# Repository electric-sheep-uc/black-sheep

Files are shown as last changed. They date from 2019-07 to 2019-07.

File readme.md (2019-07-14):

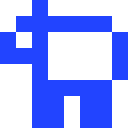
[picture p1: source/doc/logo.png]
Electric Sheep


# Electric Sheep Humanoid Robot Platform V1

This repository contains a snapshot of the
[Electric Sheep](https://humanoid.science) humanoid robotics platform as
presented in the 2019 RoboCup competition in Sydney, Australia. Please observe
the [license](LICENSE) in this repository (projects used in this release have
their own licenses either within their directories or in their source files).

We recommend that you read the technical report [here](docs/paper.pdf).

## Details

The following is intended to make understanding and using the platform easier.

**NOTE:** Vision processing will be added at a later date.

### Electronics

* [Design](docs/design-pcb.md) - Circuit design and BOM.

### Hardware

* [Design](docs/design-hw.md) - Hardware design and BOM.
* [Assembly](docs/assembly-hw.md) - Assembly of the platform.

### Source

* [Compiling](docs/compiling.md) - Compiling the `source` code.
* [Running](docs/running.md) - Running the code.

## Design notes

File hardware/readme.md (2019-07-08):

# Introduction

The initial decision is to use `openscad` [1], a CAD environment that allows
programmers to build models. There are various advantages to this model:

* The models are programmed, utilizing the majority skills of the team
* Output can be viewed at any time, with compiler warnings/errors displayed
* The source code plays nicely with `git` repositories
* Adjustments can be as simple as changing variable values
* Shapes can easily be achieved that could otherwise take a long time by hand
* Plays nicely with Linux, Windows and Mac

# Development Environment

This requires downloading `openscad` [1]. Linux users can get their latest
repository (Debian: `apt-get install openscad`).

Build models with `F6`, render the object with `F5` (in that order).

# Development Process

In general we want to build models that are justified by real measurements and
are adjustable via variables that correctly rely on one another. Improving the
accuracy of some magic value should never break any of the models if built
correctly.

If for example we decide "we want longer legs", this should be as simple as
changing a simple variable, building the models and going straight to print.
For non-experts, making changes to the models should still be very easy and
we'll likely thank ourselves in the future!

In the *future*, we should be able to simulate a robot model and leave it to
decide itself what the best simulated model is for real life performance, to
maximize some behaviour like running speed or weight.

# Building

In a Linux environment, you can run:

    bash run.sh help

This will display some available options, at the time of writing these are
building:

    bash run.sh build

To build the `.stl` files and render the `.png` files (both generated next to
the source). On the other hand, if you just want to build the STL files (which
is faster), run:

    bash run.sh build stl

**NOTE:** Files are put into a directory under `models/stl` for easier copying.
Files are given the format `<NAME>-<GIT_HASH>.stl`, where `<NAME>` is derived
from the OpenCAD filename and `<GIT_HASH>` is the first 8 characters of the
current commit. The purpose is to allow you to easily know where from random
STL files on a memory stick came from and what they are supposed to be.
Therefore, a good workflow is to pre-commit changes before running a build.

And the next option is to clean the directories:

    bash run.sh clean

Removing all binary build files (such as `.stl` and `.png`) files in the
various directories.

# References

[1] [http://www.openscad.org/](http://www.openscad.org/)

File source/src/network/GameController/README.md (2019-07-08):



# RoboCup SPL and Humanoid League GameController

This is the GameController further developed by the Humanoid League based
 on the GameController from the SPL Team B-Human

If there are any questions, please contact [sheepsy90@gmail.com](sheepsy90@gmail.de).
Please read this README carefully to avoid questions that are already answered within the document
or the [TCM](TCM.md). 

For questions regarding the protocol please check the [Wiki](https://github.com/RoboCup-Humanoid-TC/GameController/wiki).

The sources mentioned in some sections of this document are available at
[https://github.com/RoboCup-Humanoid-TC/GameController](https://github.com/RoboCup-Humanoid-TC/GameController).

### Upcoming changes (2018)

- [x] Removal of Illegal Defense and Illegal Attack
- [x] Allow Adult league to play drop in 2 vs. 2
- [x] Skip extra time in knockout games
- [x] Fix point counting on drop in challenge
- [x] Fix "GameController goes to extended time even in normal mode"
- [x] Highlight and make "current goalkeeper" changeable in UI

_See [CHANGELOG](CHANGELOG.md) for more details and history._

### Acknowledgement

The development was partially supported by the RoboCup Federation within the
calls for Support for Projects for League Developments for 2013, 2015 and 2017.

## 1. Building from Source

To build it from the source code you may use Apache Ant.
Just call "ant" in the main directory.

Building the source code requires the JDK 1.8 or newer.

## 2. GameController

### Executing the Jar

Double-click GameController.jar or run 

Usage: 
```bash
cd build/jar
java -jar GameController.jar {options}
```

    (-h | --help)                   display help
    (-t | --test)                   use test-mode - currently only disabling the
                                    delayed switch to playing in SPL
    (-i | --interface) <interface>  set network interface (default is a
                                    connected IPv4 interface)
    (-l | --league) (spl | spl_dropin | hl_kid | hl_teen | hl_adult)
                                    select league (default is spl)
    (-w | --window)                 select window mode (default is fullscreen)

### Start Dialog

Select your league. The default can be specified as a command line parameter
(see above).

Pick the two teams that are playing. They have to be different teams. If you are
practicing alone, use the "Invisibles" as second team.

SPL: The GameController automatically selects the jersey colors as defined in
the file "teams.cfg". The left teams jersey color is picked first regardless if
it has a custom jersey or not. For both teams, the first jersey color that they
have and, if picking second, that does not conflict with the jersey color of the
opponent is selected in the following sequence:

* Left team: custom 1, custom 2, blue, red
* Right team: custom 1, custom 2, red, blue

The GameController operator can switch each teams color to their secondary color
if it is necessary to distinguish the jersey colors.

You also have to select whether you play a game in the preliminaries or a
play-off game. In the preliminaries the clock will continue to run during game
stoppages and there will be no penalty shootout in case of a draw. In play-off
games, the clock will be stopped and there may be penalty shootout.

HL: You also have to select whether you play a normal game or a knock-out game.
A knock-out game will continue after a draw with two halves of extra time (if
goals were scored before) and then a penalty shoot-out if necessary. You can
also select whether teams exchange their colors in the halftime.

You can select whether the GameController should run in fullscreen mode or in
windowed mode. Note that the fullscreen mode does not work correctly on some
Linux desktops, because although they report to Java that they would support
this feature, they do not.

### Main Screen

The use of the main screen should be rather obvious in most cases. Therefore, we
only focus on the specialties.

When ever you made a mistake, use the undo history at the bottom of the screen
to correct it. You cannot correct individual decisions (except for the last
one). Instead, you can only roll back to a certain state of the game. Click the
oldest decision in the history you want to undo. After that all decisions that
would be undone will be marked. Click the decision again to actually undo it
together with all decisions that followed.

To penalize a robot, first press the penalty button, then the robot button. The
only exception is the state "Set" in playoff games, in which the "Motion in Set"
penalty is preselected and robots can be penalized by simply clicking on them
(selecting other penalties is still possible). For unpenalizing a robot, just
press the robot button.  A robot can only be unpenalized, when its penalty time
is over or when the game state changes (SPL only). Ten seconds before the
penalty time is over, the robot's button starts flashing yellow. For regular
penalties, it continues to flash until the button is pressed. Only buttons of
robots that were requested for pickup stop flashing after ten seconds and simply
stay yellow until they are pressed, as a reminder that the robot can return as
soon as it is ready. Robots with a "Motion in Set" penalty stay on the field and
will be automatically unpenalized 15 seconds after pressing the button "Play". 

Before unpenalizing a robot that was taken off the field, please make sure that
it was put back on the field by the assistant referees. For that reason, robots
are never unpenalized automatically.

To substitute a robot, press "Substitute" and then the robot that should leave
the field.  Afterwards, any of the substitutes can be activated. If the robot
that is replaced is already penalized, its substitute inherits the penalty. If
it is not, the substitute can immediately enter the field in the HL, but gets a
"request for pickup" penalty before it can enter the field in the SPL.

When pressing the big "+" (goal), "Timeout", or "Global Game Stuck", the other
team gets the next kick-off.

SPL: When the referee decides that too much game time has been lost, use the
thin "+" next to the clock to increase the game time in one-minute steps. This
is only available during stoppages of play.

### Penalty Shootout

In the penalty shootout, press "Set" and place the robots in their correct
locations. Press "Play" to start a single shot. The penalty shot is ended by
either pressing "+" for the penalty taker or by pressing "Finish" if the shot
failed. In both cases, a penalty shot ends in the state "Finished". Press "Set"
again to start the next shot.

### Shortcuts

While the GameController is running, you may use the following keys on the
keyboard instead of pushing buttons:

    Esc       - press it twice to close the GameController
    Delete    - toggle test-mode (everything is legal, every button is visible
                and enabled)
    Backspace - undo last action

only SPL

    B    - out by blue
    R    - out by red
    Y    - out by yellow
    K    - out by black
         - the new team colors implemented for RoboCup 2016 do not yet have a key
           assigned

    P    - pushing
    L    - leaving the field
    I    - fallen / inactive / local game stuck
    D    - illegal defender
    G    - kickoff goal 
    O    - illegal ball contact
    U    - request for pickup
    C    - coach motion
    T    - teammate pushing
    S    - substitute

only Humanoid-League

    B    - out by blue
    R    - out by red

    M    - ball manipulation
    P    - physical contact
    A    - illegal attack
    D    - illegal defense
    I    - service / incapable
    S    - substitute

### Adding teams to the GameController

The teams registered in the GameController are determined using the config file
located at `config/<league name>/teams.cfg` relative the the GameController.jar.
To add teams to it, lines composed of `<team number>=<team name>` may be added
to this file.
Optionally, the primary and secondary team colors may be added behind the team
name, separated by commas.

Team logos lie in the same directory as the config file with the corresponding
team number as the file name.

## 3. GameStateVisualizer

As of the 2017 RoboCup competitions, the GameStateVisualizer has been replaced
by the GameStateVisualizer mode of the TeamCommunicationMonitor.

To start it, run

`java -jar TeamCommunicationMonitor.jar --gsv`.

## 4. TeamCommunicationMonitor

The TeamCommunicationMonitor (TCM) is a tool for visualizing the data
communicated by robots during SPL games.

It serves two main purposes:

1. offering diagnostic data such as which robots are communicating on which
   team ports and whether the data that is sent by these conforms to the
   SPLStandardMessage, which is the standard communication protocol in the SPL
2. visualizing the data that was sent via SPLStandardMessages in both textual
   and graphical form.

For more info see [TCM](TCM.md).

## 5. libgamectrl (SPL)

libgamectrl automatically provides the GameController packets in ALMemory. 
It also implements the return channel of the GameController. It handles the 
buttons and LEDs according to the rules (with a few additions).

### Installation

Put the file libgamectrl.so somewhere on your NAO and add the library to your
file "autoload.ini" so that NAOqi can find it. The binary provided was built for
NAOqi 2.1.

It is also possible to build the library from source using Aldebaran's qibuild
framework. The qiproject.xml and CMakeList.txt have been placed in libgamectrl's
source folder. Just follow the instructions of the README file there.

### Usage

In your NAOqi module, execute the following code at the beginning (only once):

    AL::ALMemoryProxy *memory = new AL::ALMemoryProxy(pBroker);
    memory->insertData("GameCtrl/teamNumber", <your team number>);
    memory->insertData("GameCtrl/teamColour", <your default team color>);
    memory->insertData("GameCtrl/playerNumber", <your robot's player number>);

The team number must be non-zero. Setting the team number will reset libgamectrl
(i.e. go back to the initial state). libgamectrl will also set
"GameCtrl/teamNumber" back to zero, so it will recognize the next time your
application is started.

Setting the default team color can actually be omitted now. In that case, it is
black, i.e. the corresponding foot LED is switched off.

You can receive the current GameController packet with:

    RoboCupGameControlData gameCtrlData; // should probably zero it the first time it is used
    AL::ALValue value = memory->getData("GameCtrl/RoboCupGameControlData");
    if (value.isBinary() && value.getSize() == sizeof(RoboCupGameControlData))
        memcpy(&gameCtrlData, value, sizeof(RoboCupGameControlData));

### Deviations from the Rules

The first time the chest button is pressed it is ignored, because many teams 
will use it to let the robot get up.

In the Initial state, it is also possible to switch between "normal", 
"penalty taker" (green LED), and "penalty goalkeeper" (yellow LED) by pressing 
the right foot bumper. The state is shown by the right foot LED, and only in 
the Initial state. An active GameController will overwrite these settings.

## 6. Coach Messages

The coach broadcasts messages as defined in SPLCoachMessage.h to the UDP port
SPL_COACH_MESSAGE_PORT through the wireless network. Players are not permitted
to listen to this port. The GameController will integrate the coach messages
into the RoboCupGameControlData packet and forward them to the players according
to the SPL rules. Since coach messages must be human readable, it is assumed
that they are a zero-terminated string and all data after the first zero
character is zeroed, too.

The GameStateVisualizer also displays the coach messages.

Please note that the field "team" now contains the team number, not the color.

## 7. Protocol

For questions regarding the protocol please check the [Wiki](https://github.com/RoboCup-Humanoid-TC/GameController/wiki).

## 8. Known Issues

There are still a number of issues left:
  
- The qibuild file for libgamectrl is untested.

- The alignment of button labels is bad if the buttons are small.

- The GameController is not displaying properly on Windows-High-Res-Systems.

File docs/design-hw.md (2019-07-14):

# Design (Hardware)

For the platform, we had several requirements:

1. The platform must be low-cost. The reason for this was two-fold, firstly our
team operates on a relatively low-budget and secondly the cost-to-entry into
the RoboCup humanoid league has been gradually increasing (many platforms are
easily more than 10k euros each for a single robot). We believe that it's still
possible for low-cost entries to make a large impact in the league and hope
that this release will add to such efforts.
2. It must be easy (relatively speaking) to design and build. None of our team
are electrical engineers, for a while we didn't have any 3D designers and only
a few with any kind of background in robotics. Using off-the-shelf components
as much as possibly greatly reduces the risk in such an ambitious project.
3. The platform must be open-sourced at the end, regardless of performance in
the competition. If somebody decided to replicate our work then we need to be
able to beat our past selves in order to progress year-on-year. We also hope
that we are able to make some small contribution to the future success of the
leagues (even if this be a lesson in what not to do).

We decided on the following features:

* Raspberry Pi 3B as a main board - it offers just about enough computational
power for simple behaviours, but most importantly it's well understood and
doing low-level hardware communications is relatively simple.
* Large PWM motors for arms - As the arms are barely used in most games and
mostly used for standing after a fall, we decided if anywhere we were to use
cheaper motors, it would be here. PWM motors have a horrible habit of being
twitchy at the best of times, but especially when the PWM signal is noisy. The
cost of these motors is somewhere between a fifth and a tenth of their smart
motor counterparts.
* Smart motors for legs - We did decide that at least some accuracy was
required in the system, especially for walking. The obvious choice was
magnetically encoded smart motors that daisy-chain power and communicate on a
serial bus.
* Standard voltage step-down converters - The final voltage out of the power
PCB was much higher than we wanted for our components, so step-down is
required. We decided not to design/build our own as power system design tends
to be some form of magical art.

## BOM

The following are components used in our build:

* [IMU](https://www.banggood.com/6DOF-MPU-6050-3-Axis-Gyro-With-Accelerometer-Sensor-Module-For-Arduino-p-80862.html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)
* [Header Connectors](https://www.banggood.com/10X-2AWG-60-Core-30cm-Male-to-Male-Futaba-Plug-Servo-Extension-Wire-Cable-Parallel-Cable-p-1102386.html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)
* [Raspberry Pi 3 B](https://www.banggood.com/Raspberry-Pi-3-Model-B-ARM-Cortex-A53-CPU-1_2GHz-64-Bit-Quad-Core-1GB-RAM-10-Times-B-p-1041862.html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)
* [T60 Battery Connector](https://www.banggood.com/5Pcs-30cm-Battery-ESC-XT60-Plug-Extension-Wire-Cable-Male-Female-p-1090915.html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)
* [DC Barrel Female](https://www.banggood.com/10pcs-5_5-x-2_1mm-DC-Power-Supply-Female-Jack-Socket-p-1062018.html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)
* [Power Switch](https://www.banggood.com/2Pin-15A-250V-AC20A-125V-AC-Gas-Generator-Kill-Stop-Run-Switch-Fr-Wen-Power-Pro-p-1242672.html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)
* [Large PWM Motor](https://www.alibaba.com/product-detail/Feetech-FITEC-FS6535M-30kg-High-Torque_60200752064.html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) x 6
* [Smart Motor](https://www.alibaba.com/product-detail/FEETECH-SM30-360T-M-Serial-s_60638962033.html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) x 12
* [Fuse Holder](https://www.banggood.com/Waterproof-Car-Auto-10-15-20-30A-Amp-In-Line-Blade-Fuse-Holder-Fuses-p-916113.html?ID=45357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)
* [Micro USB Cable](https://www.banggood.com/Bakeey-3A-Micro-USB-Braided-Fast-Charging-Cable-28cm-For-Xiaomi-Redmi-Note-4-4x-Samsung-S7-Edge-S6-p-1234852.html?ID=512288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)
* [PWM PSU](https://www.banggood.com/8A-24V-TO-12V-Step-down-LED-Driver-Adjustable-Power-Supply-Module-p-927773.html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) x 2
* [Raspberry Pi Cooling](https://www.banggood.com/CNC-V3-Aluminum-Alloy-Armor-Protective-Case-Dual-Cooling-Fan-Kit-For-Raspberry-Pi-3-Model-B-3BPlus-p-1456092.html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)
* [Voltage Monitor](https://www.banggood.com/2-6S-Lipo-Battery-Low-Voltage-Tester-Buzzer-Alarm-For-RC-Model-p-1213452.html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)
* [DC Fan](https://www.banggood.com/5000rmin-DC-12V-Motorcycle-Radiator-Charger-Cooling-Fan-Humidifier-Electric-Cooler-5x5cm-p-1133447.html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) x 2
* [Relays](https://www.banggood.com/5V-2-Channel-Relay-Module-Control-Board-With-Optocoupler-Protection-For-Arduino-p-1142262.html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)
* [PWM Motor Controller](https://www.banggood.com/PCA9685-16-Channel-12-bit-PWM-Servo-Motor-Driver-I2C-Module-For-Arduino-Robot-p-1170343.html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)
* [Smart Motor Controller](https://www.alibaba.com/product-detail/Multi-function-serial-port-signal-converter_60707270225.html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)
* [LiPo Battery (T60)](https://www.alibaba.com/product-detail/Factory-price-40C-14-8V-2200mah_60831078917.html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)
* [Push Buttons](https://www.alibaba.com/product-detail/DIY-Kit-1x4-4-Independent-Key_60772024013.html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)
* [DC Supply (Laptop Adapter)](https://www.banggood.com/96W-Universal-AC-Adapter-Power-Supply-Charger-Cord-For-Laptop-Notebook-p-1131283.html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)
* [Balanced Charger](https://www.banggood.com/Wholesale-IMAX-B6-Digital-RC-Lipo-NiMH-battery-Balance-Charger-p-46220.html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)
* [Camera](https://www.banggood.com/Mini-USB2_0-12MP-1080P-HD-Pro-Webcam-Camerawith-Microphone-Mic-for-PC-p-1122462.html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)
* [USB Cable](https://www.banggood.com/30CM-Blue-Male-USB-2_0A-To-Mini-Male-USB-B-Cable-For-Arduino-p-999008.html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)
* [Micro SD Card](https://www.banggood.com/Mixza-Year-of-the-Dog-Limited-Edition-U1-32GB-TF-Memory-Card-p-1295486.html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)
* [PWM Extension Cables](https://www.banggood.com/22AWG-60-Core-20cm-Male-to-Male-JR-Plug-Servo-Extension-Wire-Cable-p-1056558.html?ID=3416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)
* [MG995](https://www.banggood.com/4X-MG995-High-Torgue-Mental-Gear-Analog-Servo-p-999629.html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)
* [MG995 Horn Mount](https://www.banggood.com/Robot-Biaxial-Servo-Spare-Part-Round-Servo-25T-Mount-Bracket-for-DIY-Robot-p-1068917.html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) x 4
* [USB Step Down Converter](https://www.banggood.com/DC-DC-Buck-Module-6-24V-12V24V-to-5V-3A-USB-Step-Down-Power-Supply-Charger-Efficiency-97_5-p-1103973.html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)

And the following optional supporting parts:

* [Ethernet Cables](https://www.banggood.com/Original-Xiaomi-Power-Strip-Fast-5-Charging-Ports-Power-Plug-AU-Standard-Plug-p-1011763.html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)
* [Ethernet Switch](https://www.alibaba.com/product-detail/High-Quality-Gigabit-Switch-16-port_60662482838.html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)
* [Additional Fuses](https://www.banggood.com/Excellway-DC003-160Pcs-Blade-Fuse-Assortment-Auto-Car-Motorcycle-Fuses-35101520253040Amp-p-1436004.html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)
* [Power Cable Red](https://www.banggood.com/DANIU-10-Meter-Red-Silicone-Wire-Cable-10121416182022AWG-Flexible-Cable-p-1170297.html?ID=520651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)
* [Power Cable Black](https://www.banggood.com/DANIU-10-Meter-Black-Silicone-Wire-Cable-10121416182022AWG-Flexible-Cable-p-1170303.html?ID=520651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)
* [JST Twin Connectors](https://www.banggood.com/10-Pairs-2-Pins-JST-Female-Male-Connector-Plug-Cable-Wire-Line-110mm-Red-p-1268119.html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)
* [Black PLA Filament](https://www.amazon.com/HATCHBOX-3D-PLA-1KG3-00-ORN-Filament-Dimensional/dp/B01FKESAMA/)
* [Nuts and Bolts](https://www.banggood.com/Suleve-M3SS2-M3-442Pcs-Stainless-Steel-Allen-Bolt-Nut-Hex-Socket-Cap-Screw-Assortment-Kit-p-1076216.html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)
* [Heat Shrink Tubes](https://www.banggood.com/Soloop-328pcs-21-Polyolefin-Halogen-Free-Heat-Shrink-Tube-Sleeving-5-Color-8-Size-p-969574.html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)
* [LiPo Safe Bag](https://www.banggood.com/DUPU-Explosion-Proof-Fire-Proof-Bag-For-Li-Po-Battery-p-950215.html?ID=3147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)

## Discussion

*For details, please see our technical report paper.*

In general we found the PWM motors (of all types) to be too large for their
power, get too hot and not be accurate enough. The support circuitry for their
required voltages, a dedicated controller and additional code to address them
requires large improvements.

If you are thinking of using this platform, please either wait or contact us
for details about version 2 - which will address many of these short comings.

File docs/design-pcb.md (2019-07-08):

# Design (PCB)

When testing our motors (sometime before the initial qualification for RC 19)
we discovered that the arm motors in particular were very power hungry. A 3 or
4 amp power supply could not even get them to move. Testing them on a 10 amp
bench power supply on the other hand delivered very solid torque. Observing the
power supply we saw that each motor could easily draw 3 amps when performing
some action under load and we ran under the assumption that not every motor
would be under full load all of the time (as the mass of the robot could be
spread across several motors). We came to a number of 10 amps budget for the 6
arm motors. Given the increased efficiency of the leg motors and considering
the fact there are 10 of them, we also assumed that 10 amps was potentially a
suitable budget. Given the need to power the main board, fans, etc, as well as
having a comfortable overhead to use, we came at a number of 30 amps supply -
but we don't believe our system will ever reach this.

We had the following requirements of the power PCB:

1. Switch between battery supply (4 cell) and DC power supply
2. Battery should not be depleted before a match
3. Battery and DC supplies should be sufficiently isolated
4. Heat generated should be distributed over a reasonable area (our chassis
begins to warp at 80 degrees)
5. The system should be fused (in our case at 20 amps)
6. Circuit should be simple and easy to understand for non-electrical persons
7. Ability to detect low battery voltage and warn the robot handler
8. The output should be greater than 12V (by some margin) to allow for suitable
step-down further on in the system (in our case, 12V for smart motors, 5V PWM
motors and 5V for mainboard logic)

With these requirements, we came to the following circuit:

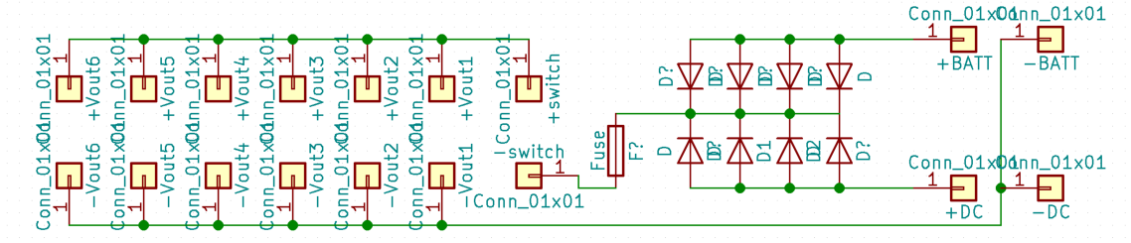
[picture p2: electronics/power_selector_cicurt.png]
PCB schematic


The traces can reasonably be expected to pass 30A through them, the diodes each
deliver 7 camps and the whole system is fused to 20A.

## Components

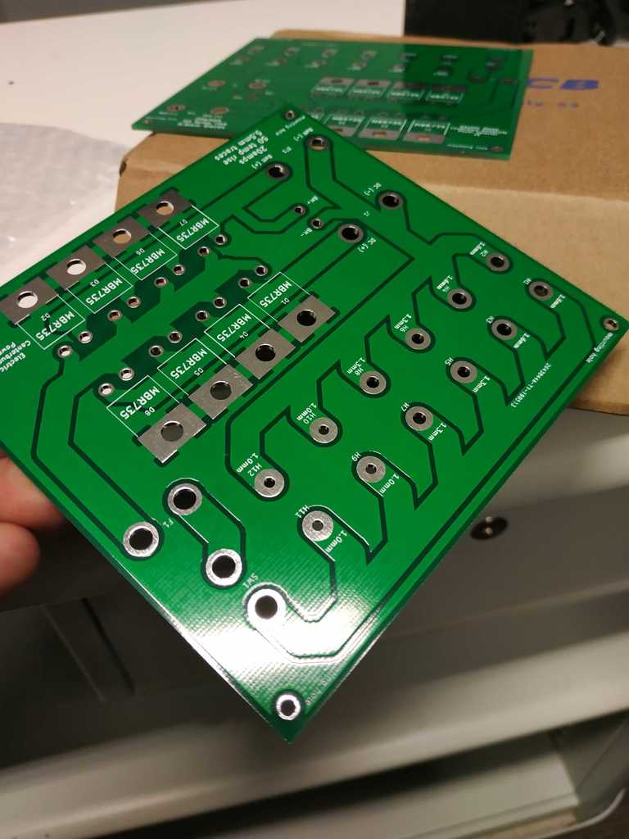
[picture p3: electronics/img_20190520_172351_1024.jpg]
PCB created


We provide the Gerber files in the source that can be sent to a PCB
manufacturer. The entire board was designed and built in KiCAD as an open
source PCB editor (the tutorials/support is very good). In order to build this
PCB you will need:

* Power cable with a suitable AWG rating (we found that automotive/marine 25A
cable is quite good - best to be sourced locally rather than online)
* [Diodes](https://www.jaycar.co.nz/diode-mbr735-schottky-35v-7a-to-220-2/p/ZR1029)
* [Power switch](https://www.banggood.com/2Pin-15A-250V-AC20A-125V-AC-Gas-Generator-Kill-Stop-Run-Switch-Fr-Wen-Power-Pro-p-1242672.html)
* [Fuse holder](https://www.banggood.com/Waterproof-Fuse-Holder-Socket-Blade-Type-In-Line-6-32V-with-10152030A-Replacement-Fuses-p-916113.html)
* [Battery connector](https://www.banggood.com/5Pcs-30cm-Battery-ESC-XT60-Plug-Extension-Wire-Cable-Male-Female-p-1090915.html)
* [DC connector](https://www.banggood.com/10pcs-5_5-x-2_1mm-DC-Power-Supply-Female-Jack-Socket-p-1062018.html)
* [Battery monitor](https://www.banggood.com/2-6S-Lipo-Battery-Low-Voltage-Tester-Buzzer-Alarm-For-RC-Model-p-1213452.html)

Additionally, we found
[this](https://www.banggood.com/96W-Universal-AC-Adapter-Power-Supply-Charger-Cord-For-Laptop-Notebook-p-1131283.html)
was a reasonably good cheap DC power supply.

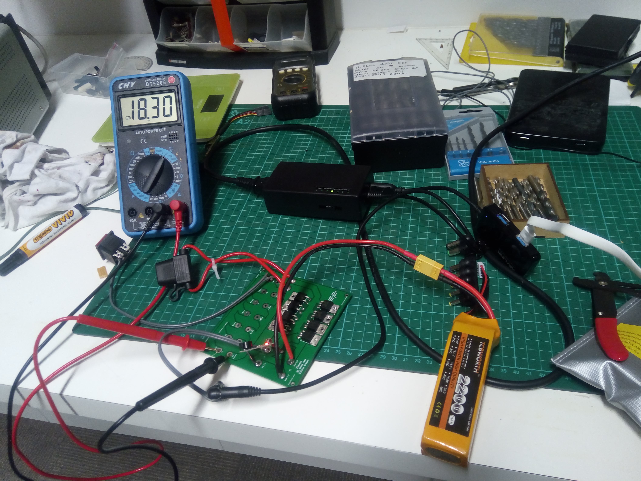
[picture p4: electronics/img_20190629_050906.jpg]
PCB soldered


## Discussion

The power PCB acted exactly as designed, we have zero complaints about it's
ability to safely deliver power to our system. At one point we decided to
over-volt our motors (thereby increasing current draw and heat), with no known
issues found in the power OCB, despite acting outside of the design parameters.
We are very confident in the simplicity of the design.

One flaw with the design is that the back plane isn't used as a heat
distribution plane, but this actually wasn't an issue as the board was cool
throughout with zero cooling. Making better use of the backside of the
two-layer PCB could have helped reduce the size of the PCB.

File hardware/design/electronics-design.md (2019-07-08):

\newpage

# Introduction

This document exists to document design decisions, as well as give information
about the hardware involved. It also allows for us to predict potential issues
and already have solutions for those.

\newpage

# Diagram

Block diagram for electronics.

Figure 1 shows a basic block diagram of how the electronics will be connected,
mostly concerning itself with supplying the correct voltage to each location.
The top number is simply an ID of the block, the second name is a generic name
and below that is either `Out`, the output voltage or `In`, the input voltage.

\newpage

# Breakdown

The following component breakdown is to allow for considerations to be made
early on with regards to what will be the required voltage in order to get the
electronics operating correctly. This allows us to make an efficient PSU (power
supply unit) and consider which part will be responsible for supplying power.

\newpage

## `[01]` Battery

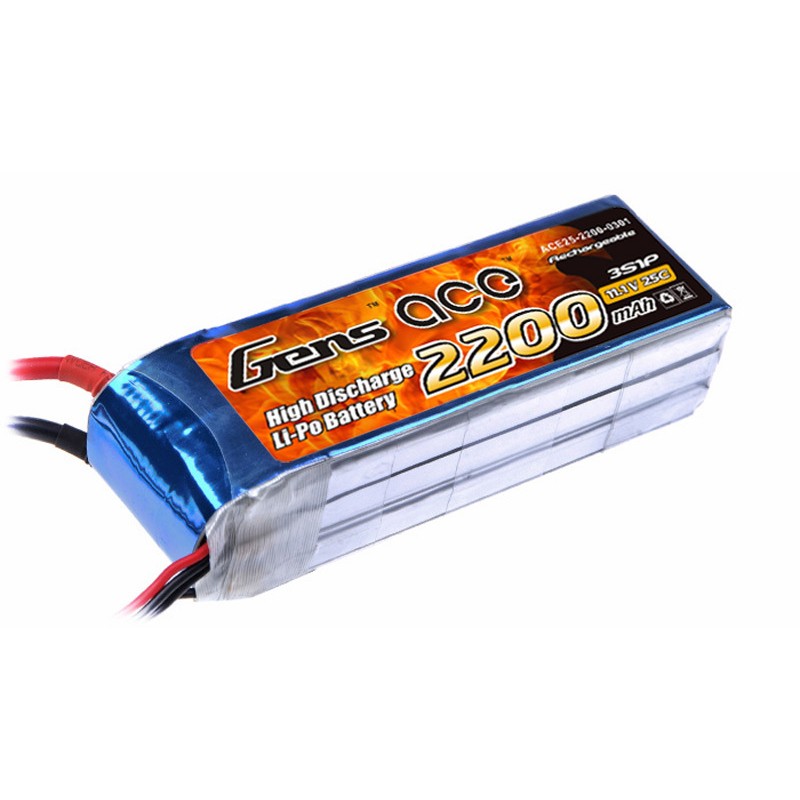
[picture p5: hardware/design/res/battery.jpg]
Example 3 cell battery.


### Requirements

* `>2000mAh` -- The robot needs to last for 10 minutes (one half of a game).
  The battery capacity must be higher that is required within that time, as the
  robots can sit a while whilst waiting for game start and power output over
  the play time is not linear. The battery's capacity will also drop over time
  due to use, possibly as low as 50%.
* `Common connector` -- Allow us to use batteries of several different types
  and find common parts.
* `Balanced charger` -- Cells must be charged and kept at the same voltage
  (with small tolerance). Largely unbalanced cells can lead to thermal runaway
  events.

### Description

**NOTE:** There is no description until the hardware is decided.

### Risks and Solutions

* *Battery damage* -- Batteries can become damage beyond repair.
  *Solution:* Battery can be discharged to `0V` and put in normal household
  rubbish without special treatment. An additional step is to twist the main
  terminals together as proof of its discharged state.
* *Battery explosion* -- Batteries can explode and catch fire.
  *Solution:* Whilst in use (charge or discharge), keep in a LiPo safe
  container/bag.
* *Cells unbalanced* -- This is where the battery voltages of each cell becomes
  different. This can cause current loops within the battery, leading to
  thermal runaway events.
  *Solution:* A balanced charger can be used to charge each cell individually.
* *Cells depeleted* -- Cells that drop down to 0V are to be considered dead, as
  this represents a large amount of damage to the battery's chemistry.
  *Solution:* Replace the battery, see "Battery damage".
* *Battery too warm* -- Batteries operating at temperatures too hot to touch.
  *Solution:* See "Battery damage". If this is considered too risky, battery
  should be dropped in a high salt solution bucket of water and left for
  several weeks in a safe place.
* *Battery bloated* -- If excessive, it can be gas trying to escape from the
  LiPo.
  *Solution:* See "Battery damage".
* *Storing batteries* -- Storing batteries for a long time can cause issues
  with the battery chemistry for later use.
  *Solution:* Discharge/charge the batteries to nominal storage voltages.

\newpage

## `[02]` Direct Current

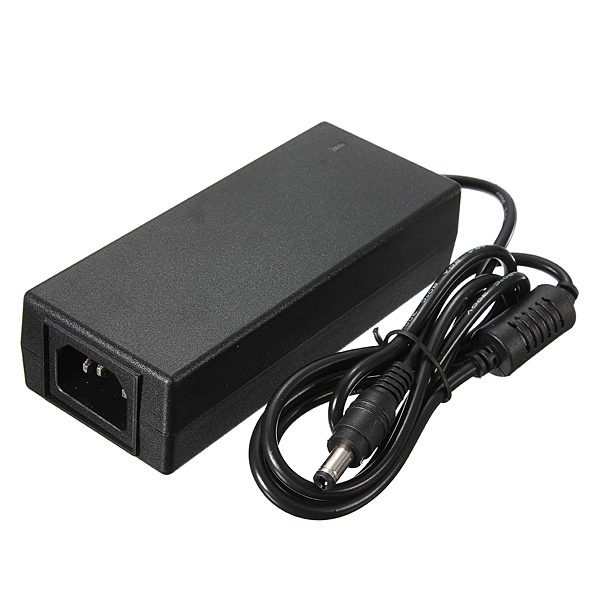
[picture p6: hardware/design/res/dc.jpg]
Example DC power block.


### Requirements

* `>5A` -- Power required to run the robot safely in mostly stand-by mode.
* `>2m` -- Length of the power cord to allow movement of the robot without
  pulling on the power socket.
* `Ground` -- The power cord should have a ground pin to prevent static build
  up. This can happen on metal parts and be dangerous the ESD (Electro Static
  Discharge) sensitive parts.

### Description

**NOTE:** There is no description until the hardware is decided.

### Risks and Solutions

* *Intermitten supply* -- When cables or connectors are starting to break, the
  output can be non-steady and create noise. This in general is not too much
  human risk, but may cause issue when changing batteries during competition as
  the robots could temporarily be without power, causing a reboot and possible
  corruption.
  *Solution:* Test the supplies and mark them as "bad" if found to be non-working.
* *Varying mains voltage* -- Travelling to different competition locations may
  mean that the input voltage varies from 240V down to 100V.
  *Solution:* Purchase units that are able to deal with the change in supplies.
* *Broken cable* -- On mains side, this is exceptionally dangerous, although
  with alternating current. DC side, the voltage is low and human body
  resistance is high, so the electric shock should be minimized.
  *Solution:* Any cables identified as bad should be purposely cut in half in
  order to prevent future use.

\newpage

## `[03]` Power Supply Unit

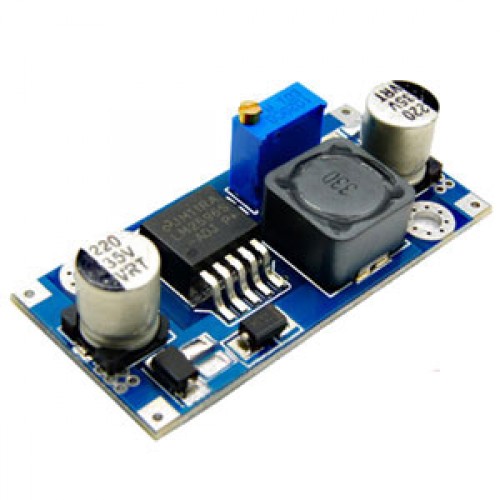
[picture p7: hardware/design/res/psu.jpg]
Example PSU.


### Requirements

* `10-20A` -- The power supply must be able to support at least 10A of constant
  current and an estimated 20A of peak current in order to keep up with the
  potential motor loads.
* `Testable` -- The power supply must be testable in order to ensure it is
  working correctly.
* `Replaceable` -- It is likely that the design will eventually break, it
  should be a design we are able to rebuild with relative ease.
* `Upgradeable` -- In the future we may need to be able to upgrade our power
  consumption as the size of our robot tends towards human. The design should
  be such that we can simply replace components with larger capacity ones and
  still be able to use the same design.
* `Constant voltage` -- The PSU must provide reliable voltage regardless of the
  DC or battery value (within reason).
* `DC-Battery switch` -- The system must automatically switch between DC power
  and battery power, with preference on battery power.
* `Power indicator` -- There must be a low power indicator for which supply is
  currently in use.
* `Low power warning` -- The system must provide warning of low power in
  audible form that can be heard from a reasonable distance.
* `Low power cutoff` -- When the battery is below a selected voltage, the power
  supply must switch off all non-essential supplies in order to prevent battery
  damage.
* `Power switch` -- We must be able to switch the power off reliably.

### Description

The result of a team discussion on the matter has lead us to strive towards
using a mostly off-the-shelf components in order to speed up the design
process. As a result the following diagram has been proposed:

PSU block diagram.

The following is a breakdown of parts:

* `[A]` (*DC Source*) -- This is the mains supply to 12V DC power converter.
* `[B]` (*Batt Source*) -- This is a three cell LiPo.
* `[C]` (*Darwin PSU*) -- This is a simple design borrowed from the Darwin OP
platform.
* `[D]` (*Buck StepDown*) -- This is for the PWM motors.
* `[E]` (*Buck StepDown*) -- This is for the smart motors.
* `[F]` (*USB PWM PSU*) -- This is for the main board.
* `[G]` (*PSU Controller*) -- This is for low battery control.

Proposed components:

* `[C]` -- Darwin OP PSU:
https://sourceforge.net/projects/darwinop/files/Hardware/Electronics/Boards/DARwIn-OP_Power.pdf/download
* `[D]`, `[E]` -- Step down buck converter:
https://www.banggood.com/3Pcs-XL4015-5A-DC-DC-Step-Down-Adjustable-Power-Supply-Module-Buck-Converter-p-1157548.html
* `[F]` -- USB power supply:
https://www.banggood.com/XH-M249-DC5V-6A-Step-Down-Module-12V24V-to-5V-Power-Supply-USB-Charging-5A-30W-p-1264861.html
* `[G]` -- Digispark:
https://www.banggood.com/Digispark-Kickstarter-Micro-USB-Development-Board-For-ATTINY85-Arduino-p-1038088.html

### Risks and Solutions

* *Power sinking* -- The battery and DC inputs should be completely isolated
  from one another. If not, there is potential for either one to be damaged.
  *Solution:* The electronics should be designed in such a way that it is
  impossible for both to be in at the same time.
* *Computer crash* -- The onboard may be in the middle of doing a write to
  disk whilst experiencing sudden loss of power, therefore opening up the
  potential to corruption.
  *Solution:* The main disk should be removable and replaceable relatively
  easily, as well as the power control offering a signal for the main board to
  shutdown safely.
* *Low battery* -- A battery that is used for a length of time may run low.
  *Solution:* Alarm for low power scenarios, followed by manual shut-off.
* *Electrostatic discharge* -- The power supply may have a DC offset either due
  to a badly earthed mains or simply from movement of the robot and rubbing of
  materials.
  *Solution:* Isolation from human interference, meaning no conductive parts
  should be touchable.
* *Heat* -- The system will likely provide a lot of heat at full power.
  *Solution:* Active calling may be required on order to prevent damage to the
  chassis.

\newpage

## `[04]` Smart Controller

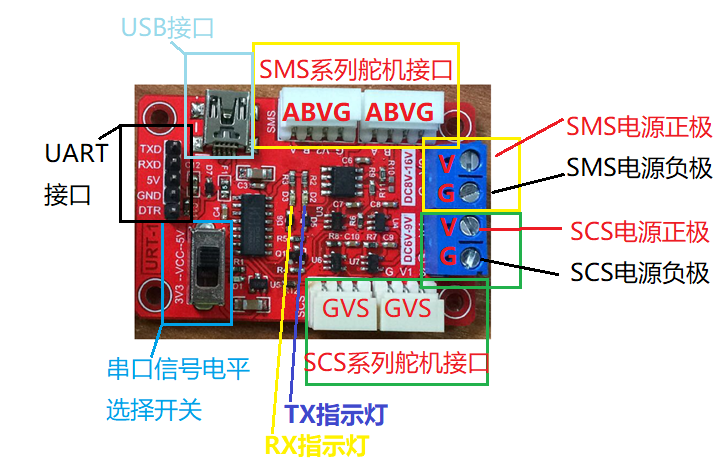
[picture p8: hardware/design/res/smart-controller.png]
Smart controller used.


### Requirements

* `Smart motor communication` -- The smart motor controller must be able to
  able to communicate with multiple smart motors.
* `Main board communication` -- The smart motor controller must be able to
  communicate with the main board, ideally via USB.
* `Position control` -- The controller must be able to update specific motor
  positions, as well as retrieve data about individual motors.

### Description

Source: https://www.alibaba.com/product-detail/Multi-function-serial-port-signal-converter_60707270225.html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

#### Quick Details

    Place of Origin: Guangdong, China (Mainland)
    Model Number:    FE-URT-1
    Type:            USB/URAT to SMS (RS485) &S...
    Quality:         Magnetic coding servo
    Color:           Red
    SHIPPING WAY:    DHL FEDEX UPS EMS TNT
    Payment term:    Paypal TT WU ESCROW
    Brand Name:      FEETECH
    Product Name:    Multi function serial port signal...
    Application:     Serial control servo
    Package:         Standard Package (plastic Bag...
    Material:        ABS
    Condition:       Brand Newand Original

#### Package & Delivery

    Packaging Details: packed with PE bag then carton box
    Delivery Time:     3 working day

#### Product Description

**Multi function serial port signal converter USB/URAT to SMS (RS485) &SCS
(TTL)**

**Overview of 1. functions**

URT-1 multifunction serial signal converter, in order to facilitate the user to
debug and use SMS and SCS composite Feite series serial servo design.

URT-1 integrated USB serial port chip, combined with linear low-voltage
differential voltage regulator circuit, USB signal can be easily converted to
5V or 3V3 serial signal level.

In the URT-1 board, serial signal conversion circuit respectively into two
different levels of signal, which A road - asynchronous half duplex RS485 level
port can be connected to the SMS series servo; B - asynchronous half duplex TTL
level single bus port can be connected to the SCS series of steering gear.

In the URT-1 board in the input and output signal by using asynchronous serial
time-sharing using hardware circuit, hardware automatic diversion, without the
use of additional IO enable to control, reduce the occupation of MCU port
burden and code simple.

USB port using USB MINI interface; UART interface with 2.54 row spacing
general; SMS series servo interface using 5264-4AW interface can be directly
connected to the steering gear; SCS series servo interface using 5264-3AW
interface can be directly connected to the steering gear.

The working voltage of SMS and SCS series servo fit is not the same, reuse
requires a different working voltage, power supply port and can also access the
SCS from the SMS section of the step-down power supply high voltage after
making the system with a power supply to provide power.

Because the power port has overcurrent limit, the maximum is 6A, so it is
necessary to do additional power distribution processing in the actual
application of the serial connection of more servos. URT-1 is only used for
signal conversion.

**2. functional features**

Full speed USB device interface, compatible with USB V2.0

Support baud rate 50bps~1Mbps

5V and 3V3 UART serial port signal level can be switched freely

Supports 32/64 bit Windows 10/8.1/8/7/VISTA/XP, SERVER
2016/2012/2008/20032000/ME/98

Microsoft digital signature authentication

SMS and SCS series servos can be shared by one serial port for control

The serial port signal is asynchronous half duplex communication mode, and the
hardware automatic diversion needs no additional enable IO

The interface of servo system adopts error proofing connection to ensure proper
connection

UART interface is general pin way, can be used as USB to serial port output,
also can connect MCU UART to control the steering gear

With signal level power indicator (D1), TX (D2) and RX (D3) indicator,
convenient to view data status

The 5V voltage is supplied from the USB, otherwise the external voltage is
supplied to the 5V

500mA overcurrent protection and overvoltage protection for USB power supply
belt

**3. specification parameters**

Weight: 12.5 grams

Size (L*W*H):55.8 * 36.6 * 11.5 mm

Mounting size: 48.8 * 28.8 mm

USB interface: MINI USB

UART interface: 2.54 pin spacing

SCS servo interface: 3PIN 5264-3AW

SMS servo interface: 4PIN 5264-4AW

Actuator power interface: 5.08 terminal

**4.motherboard port:**

Pinout diagram.

**5. need matching list**

MINI USB connection line

Power supply and line of rudder

Connecting line between steering gear and steering engine

Du Bangxian (optional)

**6. drive installation**

CH340C driver download address:

Http://www.wch.cn/download/CH341SER_EXE.html

Run the installer driver after download

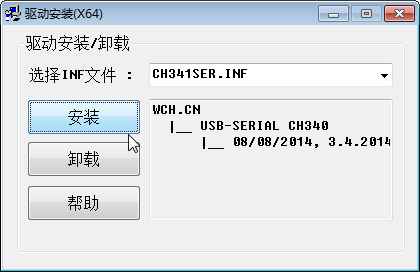
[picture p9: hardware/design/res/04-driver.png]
Driver installation.


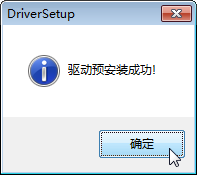
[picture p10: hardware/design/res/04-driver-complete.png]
Driver setup complete.


Click Install to wait for a period of time, do not close the installer before
prompt for successful installation.

Successfully installed or installed successfully before the driver, in the
URT-1 connection to the computer USB port, in the computer device manager can
see the corresponding port number.

**7. hardware connection**

Access the corresponding servos to the corresponding servos interface

The correct power supply is connected to the servo power supply port, in
particular, the positive and negative pole of the power supply can not be
connected

Connecting URT-1 and PC with MINI USB line

The following is a physical connection between the SMS series and the SCS
series servos, as shown below:

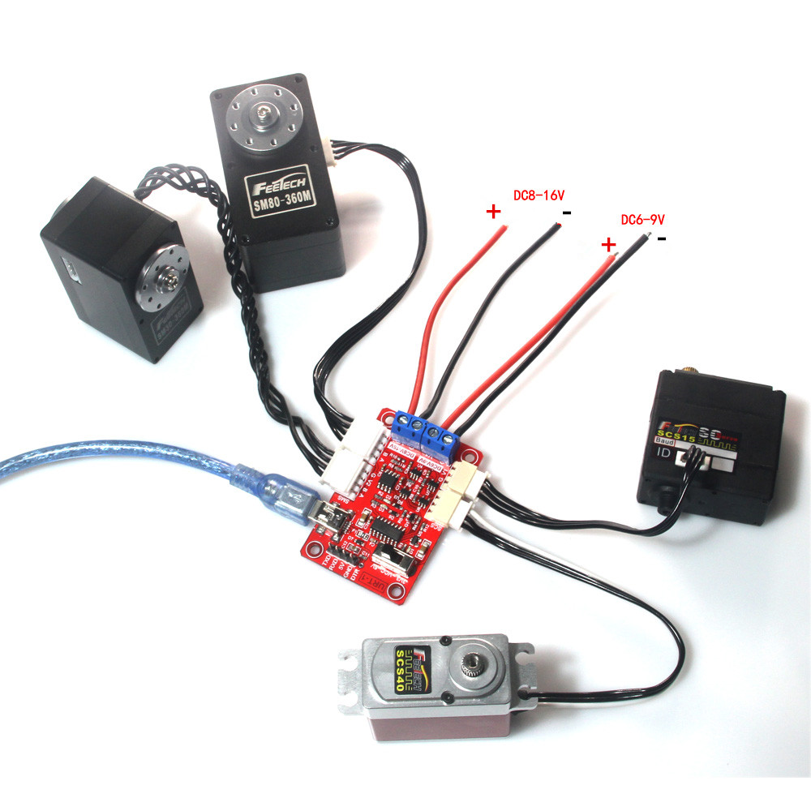
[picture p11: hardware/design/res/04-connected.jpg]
Wiring example.


**8. software testing**

Test with FD software

Debugging assistant test with serial port

### Risks and Solutions

* *Current limit hit* -- The smart motor controller has a current limit of
  `6A`.
  *Solution:* Potentially we may have to bypass the voltage supply provided by
  the board. This will require reverse engineering the power limiting circuit.

\newpage

## `[05]` PWM Controller

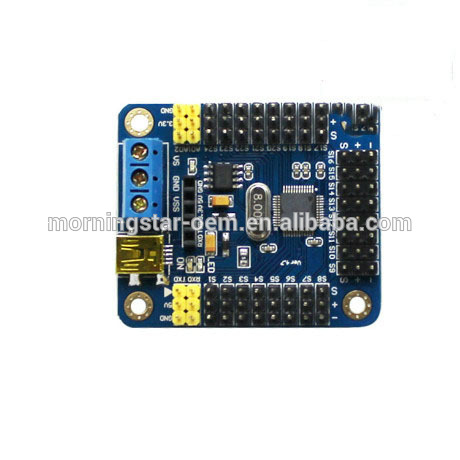
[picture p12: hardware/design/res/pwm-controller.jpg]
PWM controller used.


### Requirements

* `PWM motor communication` -- The controller must be able to communicate with
  the motors via an acceptably clean pulse width modulation input signal.
* `Main board communication` -- The controller must be able to communicate with
  the main board via USB.
* `Input voltage tollerance` -- The controller must be able to support a wide
  range of input voltages to give us flexibility.
* `Output voltage tollerance` -- A wide range of output voltages is required to
  support the two types of PWM motors that we plan to drive.
* `Individual motor control` -- We must be able to control each PWM motor
  individually.

### Description

Source: https://www.alibaba.com/product-detail/UNO-mini-USB-24-servo-control_60702742954.html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

#### Quick Details

    Place of Origin:     Guangdong, China (Mainland)
    Model Number:        MS013
    PCB size:            51mm*43.5mm*1.6mm(Mount...
    Payment:             Paypal or T/T or Western Union
    Brand Name:          MS
    Signal output:       PWM (accuracy 1us)
    Server motor dri...: 1us, 0.09 degrees

#### Package & Delivery

    Packaging Details: standard
    Delivery Time:     1 day

#### Product Description

UNO mini USB 24 servo control board Controller Servo Motor USC-24 (Line Feed)

**PRODUCT FEATURES**

1. Control chip power supply range: 6.5V ~ 12V or 4.5V ~ 5.5V. (Why there are
two ranges? Because there are two inputs) (USB can give the servo control board
chip power supply, automatic selection, with USB reverse protection, you can
protect your computer is not reverse USB voltage burned)

2. Servo part of the power supply range: DC DC (voltage and steering gear
parameters, the general use of 5V DC).

3. Control channel: control 16 at the same time. (Steering gear speed is
adjustable, the robot moves smooth and comfortable)

4. Communication input: USB or serial port (TTL, USART). (Wireless control of
the steering controller can be done using a wireless Bluetooth module or other
wireless module)

5. Signal output: PWM (accuracy 1us).

6. Servo motor drive resolution: 1us, 0.09 degrees.

7. Baud rate range: 9600 19200 38400 57600 115200 128000. (Fully automatic
identification, no need to set)

8. Support the servo motor: Futaba or Hitec and domestic brands such as
Huisheng, etc., spike all use PWM signal control of the steering gear.

9. PCB size: 51mm x 43.5mm x 1.6mm (mounting hole spacing: 42 * 35.5mm).

10. Control mode: USB and serial (TTL) to accept the command mode. (With USB
data cable and host computer control software, software can be upgraded at any
time)

11. flash: Onboard 512K ROM. (If each command is to control the 32 steering gear
at the same time, you can save more than 500 instructions, if the order is very
short, save thousands of questions is not a problem)

**PRODUCT PICTURES**

Overview of device.

### Risks and Solutions

* *High current* -- It's possible that if we draw too high a current that we
  burn out the PCB traces.
  *Solution:* Prevent prolonged high current draw situations. This could be
  monitored for in the PSU controller, as high current draws will likely drop
  the supply voltage.
* *Update rate* -- Motors may be updated too slowly, causing jitter (which can
  be dangerous).
  *Solution:* Prioritize motor updates if required in order to guarantee a
  minimum refresh rate for important/potentially dangerous motors.
* *Update corruption* -- Changing from one motor position to another may cause
  the PWM signal to be corrupted, which could be dangerous for a 30kg/cm motor
  to suddenly jump to a random position.
  *Solution:* The selected motor position shouldn't be changed too drastically
  in the code, we should plot positions over time to prevent sudden jumps.

\newpage

## `[06]` Main Board

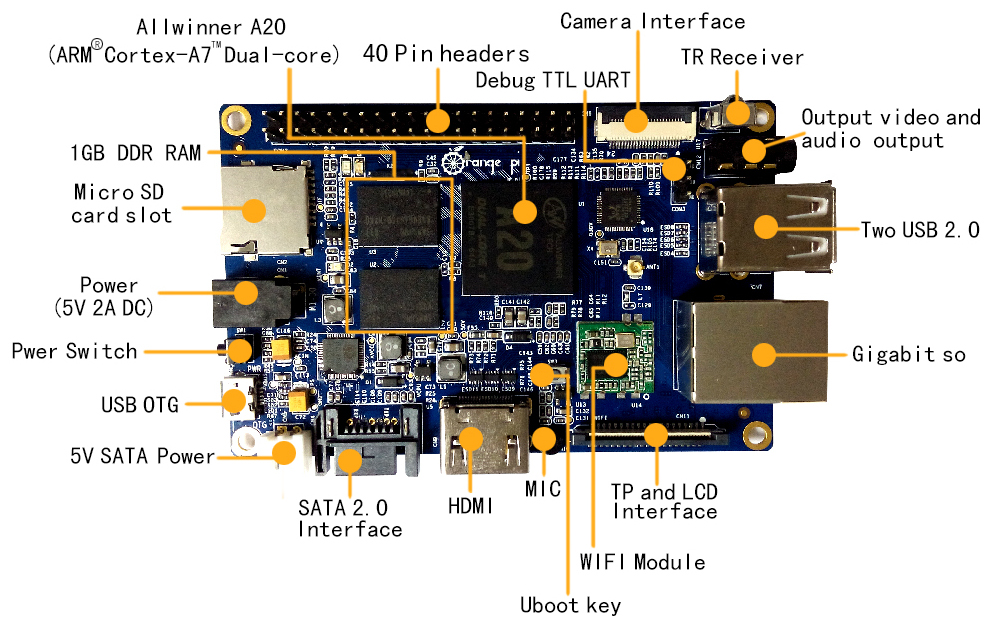
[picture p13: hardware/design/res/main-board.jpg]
Example of main board.


### Requirements

* `CPU` -- We will need a multi-core, lower power, high speed processor. It is
  likely this will either be an Intel Atom or an ARM processor. Intel has the
  advantage of being easier to compile for, but the disadvantage of being more
  expensive.
* `RAM` -- We will likely need at least `1GB`, the more the better. There's
  little benefit to having more than `4GB` for a high speed application as
  memory shouldn't be held onto from previous states.
* `Memory` -- We will need at least `4GB` of storage, `16GB` ideally. This
  should be in the form of removable memory. This will contain our code, an
  operating system and logs. It is likely to be in high use, so must also be
  relatively fast memory.
* `USB` -- We will need to connect web-camera, smart motor controller, PWM
  motor controller and PSU controller. This requires four USB ports.
* `Video` -- At times it may be required to physically access the computer (for
  cases such as networking issues via SSH). HDMI is the best all-round standard
  at this current time.
* `Power Supply` -- It should be able to support 5V with tolerance (4.5V to
  5.5V), otherwise a DC input of 9V or more.
* `WiFi` -- We will need the use of WiFi to communicate with the game
  controller.
* `Ethernet` -- Manual connection to robot for pushing code and/or changing
  settings for games/development.

### Description

**NOTE:** There is no description until the hardware is decided.

#### Product Description

### Risks and Solutions

**NOTE:** Computers are considered to be a relatively solved problem.

\newpage

## `[07]` LEDs

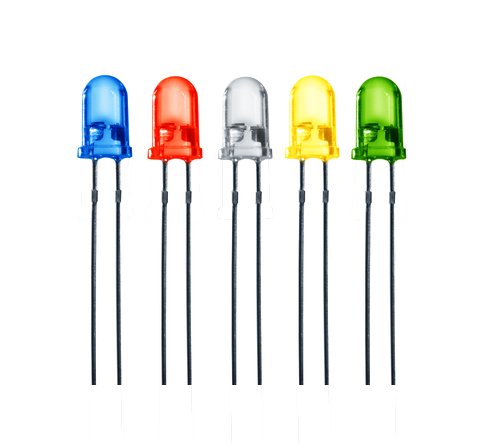
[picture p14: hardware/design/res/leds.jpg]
Example of LEDs .


### Requirements

* `Low power` -- Should not consume much current.
* `RGB` -- Should be able to output multiple colours for the purpose of
  debugging visually when physical access is not possible.

### Description

**NOTE:** There is no description until the hardware is decided.

### Risks and Solutions

**NOTE:** LEDs are a well understood Science.

\newpage

## `[08]` Smart Motor

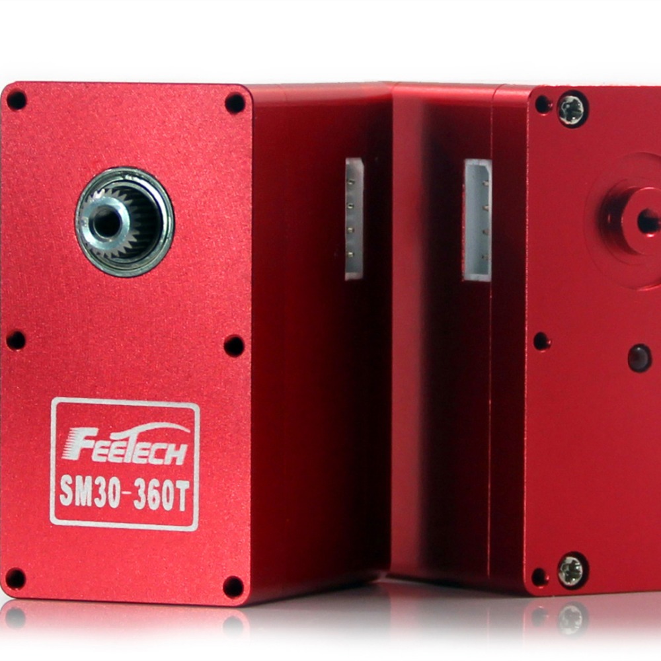
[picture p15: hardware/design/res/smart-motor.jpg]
Smart motor used.


### Requirements

* `` --
* `` --
* `` --
* `` --
* `` --
* `` --
* `` --

### Description

Source: https://www.alibaba.com/product-detail/FEETECH-SM30-360T-M-Serial-bus_60638962033.html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

#### Quick Details

    Style:              Radio Control Toy
    Power:              Battery
    Scale:              1:5
    Place of Origin:    Guangdong, China (Mainland)
    Model Number:       SM30
    metal gears:        for robot wheel
    type:               metal gears servo
    use:                Small humanoid robot
    rotation range:     0-360
    control system:     digital
    Type:               Car
    Material:           METAL
    Radio Control S...: RC Model
    Brand Name:         feetech
    large 30kg:         robot
    Bearring:           2BB
    color:              red
    fit:                Track drive
    Certificate:        ROHS

#### Package & Delivery

    Packaging Details: -Servo*1PCS
                       -Servo arm*1 bag
                       -GW:199g
    Delivery Time:     Shipped in 5 days after payment

#### Product Description

**FEETECH SM30  Robot  servos for more than 30 kg in 180-360 degree**

SM30-360T/M  Serial bus smart control servo fully integrated Motor, servo
drive,

Serial bus communication interface and sensor together as one servo,Mainly used
for micro robot joint, wheel, track drive,

Can also be used for other simple position control occasions.

Feature:

Big Torque:30Kg. cm

Large Angle:+-30 thousand turns(Arbitrary absolute relative)

DC 6.5V~13V power supply

0.088 degrees Position resolution

Dual output shaftfit for robot joint

High precision all metal gear set,Double ball bearing

Full Aluminium alloyCNC case,Good cooling effect

Position servo control mode ,rotation range 0-360 degrees and many turns
Arbitrary absolute relative angle.

In the speed control mode ,can be continuous rotation,adjust speed

Duplex asynchronous T T L  / 4 8 5  Communication level

Daisy chain connection, 254 ID can choose

High reach  1M  Baud  rate

333Hz servo update rate

Can give feedback on  position,temperature,voltage,speed and  current load

Use open  FT SCS Serial asynchronous communication protocol

SM30-360T/M robot servo adopts advanced servo control technology and 32 bit
high speed ARM microprocessor, fast response, accurate positioning without
jitter. Compared to the traditional RC servo 50Hz control frequency, the
SM30-360T/M series robot servo through the control frequency of up to 333Hz, to
ensure the accuracy of position control and maintain the stability of the
moment.

The SM30-360T/M robot servo uses 12 bits high precision magnetic encoder to
measure the position, the servo output shaft may rotate continuously for a
whole week, the movement torque output is as high as 30kgf.cm.

SM30-360T/M has serial bus interface, the 254 robot servo can form a chain
through the bus. Each servo can be set with different node addresses, multiple
servo wheels can be unified motion can also be a single independent control.

The communication instruction set of SM30-360T/M is completely open, and the
servo communicates with the host computer through the asynchronous serial
interface. The SM30-360T/M can be set to either the motor mode or the position
control mode by sending commands through the asynchronous serial interface.

In motor mode, SM30-360T/M can be used as DC motor, speed adjustable; in
position control mode, 0-360 degrees and multi circle arbitrary absolute and
relative angle can be controlled within this range with accurate position
control performance, speed control.

SM30-360T/M robot servo and the founder of the multi - directional
installation, user-friendly flexible model.

Front view of motor.

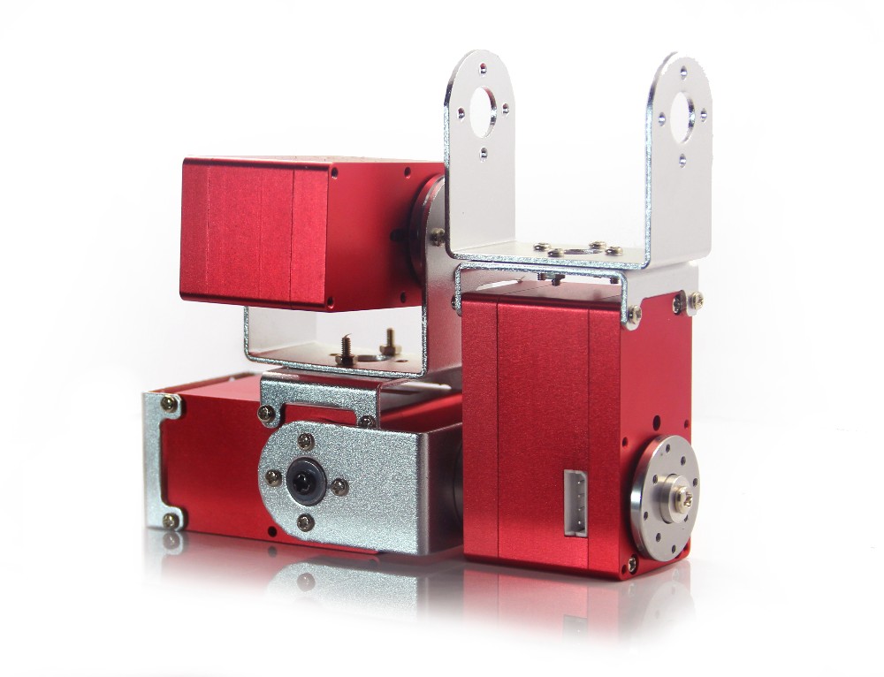
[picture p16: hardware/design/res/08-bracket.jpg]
Motor with bracket.


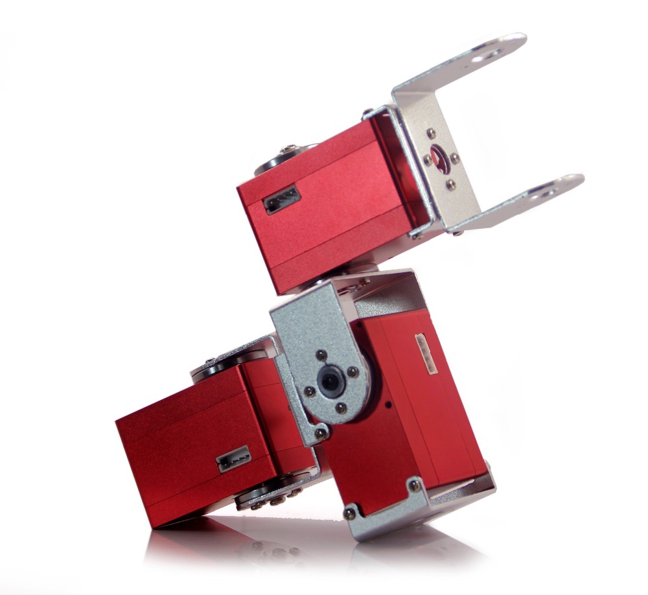
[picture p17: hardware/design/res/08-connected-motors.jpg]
Motor with bracket.


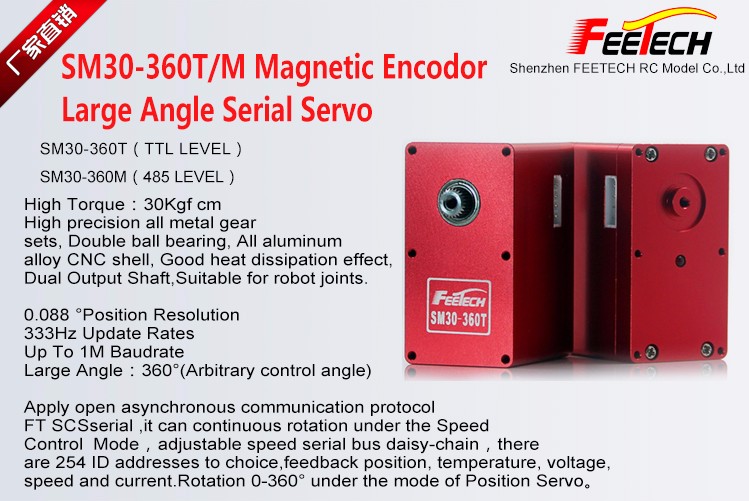
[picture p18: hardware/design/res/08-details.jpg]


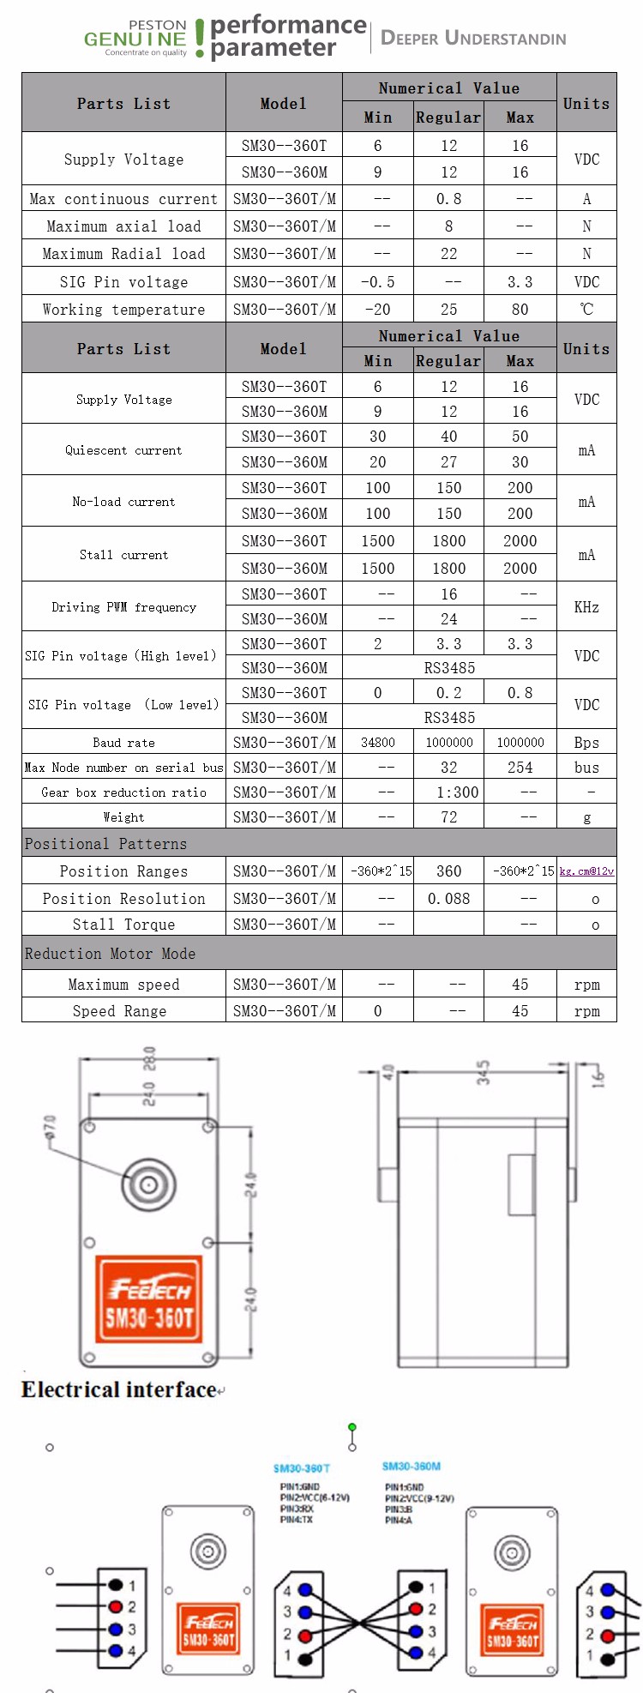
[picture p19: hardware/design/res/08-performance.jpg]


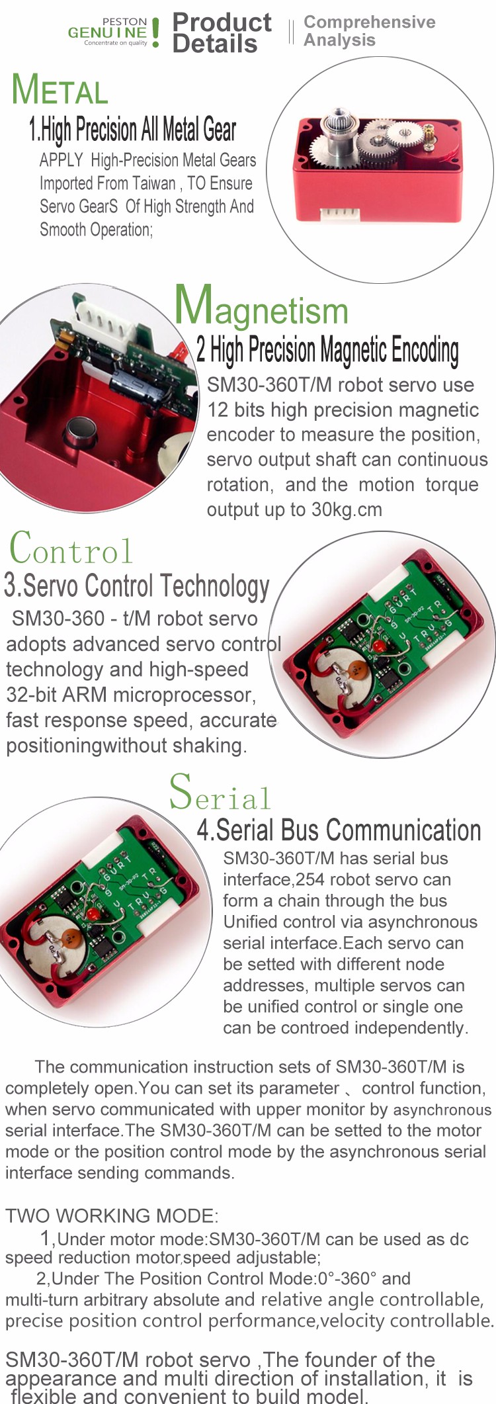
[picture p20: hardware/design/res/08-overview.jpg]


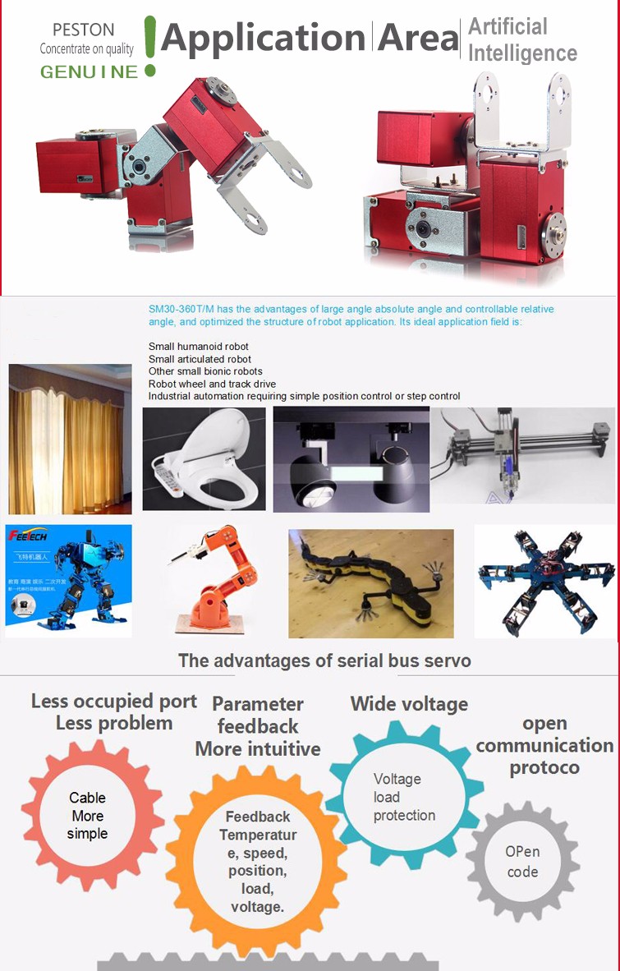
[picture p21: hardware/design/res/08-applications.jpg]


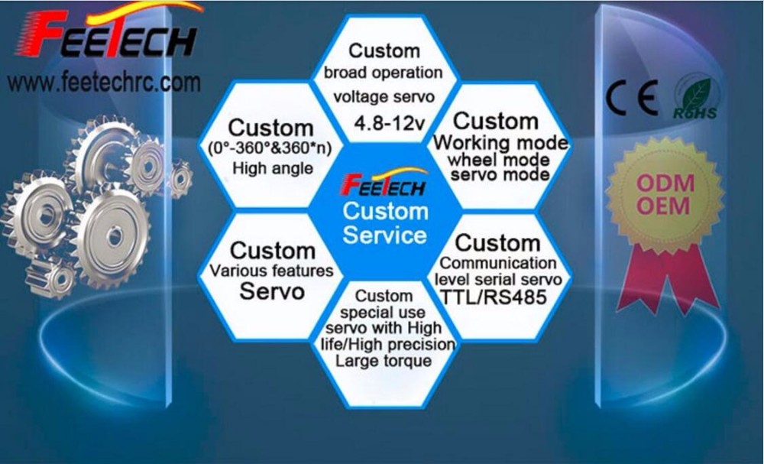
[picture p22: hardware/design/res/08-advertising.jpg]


### Risks and Solutions

* ** --
  *Solution:*
* ** --
  *Solution:*
* ** --
  *Solution:*
* ** --
  *Solution:*
* ** --
  *Solution:*
* ** --
  *Solution:*
* ** --
  *Solution:*

\newpage

## `[09]` PWM Motor MG995

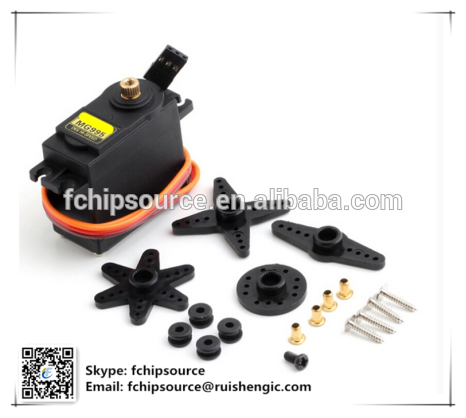
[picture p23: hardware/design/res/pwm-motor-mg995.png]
PWM motor MG995 used.


### Requirements

* `` --
* `` --
* `` --
* `` --
* `` --
* `` --
* `` --

### Description

Source: https://www.alibaba.com/product-detail/Original-Servo-MG996R-MG946R-MG995-MG945_60569740899.html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

#### Quick Details

    D/C:             2016+
    Model Number:    MG996R MG946R MG995 MG...
    Brand Name:      Original Brand
    Shipping by:     DHL\UPS\Fedex\EMS\HK Post...
    Weight:          55g
    Package:         Servo
    Type:            Servo
    Place of Origin: Guangdong, China (Mainland)
    Size:            40.7*19.7*42.9mm
    voltage:         4.8V-7.2V

#### Package & Delivery

    Packaging Details: / Cartoon
    Delivery Time:     1-2 days

#### Product Description

**Servo MG996R MG946R MG995 MG945 55g**

**Metal standard steering gear**

Overview of motor package.

Size: 40.8 * 20 * 38 mm

Weight: 55 g

Speed: 4.8 v 0.19sec / 60 degrees

6.0 v 0.18sec / 60 degrees

Torque: 4.8 V  9 kg - cm

V  11 kg - 6.0 cm

Voltage: 4.8 V to 4.8 V

No-load current work: 120 ma

Locked-rotor working current: 1450 ma

The response time of pulse width: 5 or less usec

Error in angular deviation: back to 0 degrees, 45 degrees around each 3 degrees
or less error.There are 90-360 degrees

Gear: 5 metal gears

Cable length: 300 mm

Interface specifications: JR/FP gm.

There are three lines define the steering gear:

Dark grey: GND

Red: 4.8 7.2 V to VCC

The orange line: pulse input

### Risks and Solutions

* ** --
  *Solution:*
* ** --
  *Solution:*
* ** --
  *Solution:*
* ** --
  *Solution:*
* ** --
  *Solution:*
* ** --
  *Solution:*
* ** --
  *Solution:*

\newpage

## `[10]` PWM Motor FS6535

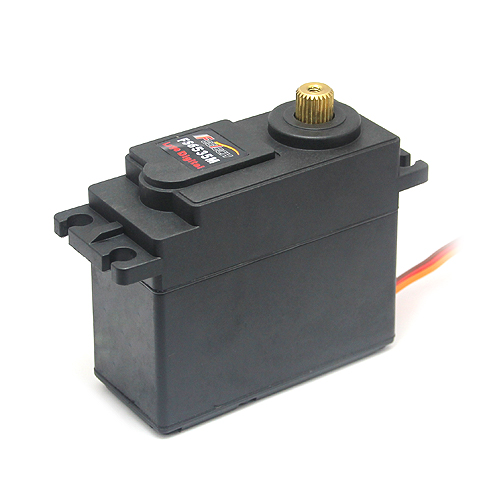
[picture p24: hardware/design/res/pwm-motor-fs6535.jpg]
PWM motor FS6535 used.


### Requirements

* `` --
* `` --
* `` --
* `` --
* `` --
* `` --
* `` --

### Description

Source: https://www.alibaba.com/product-detail/Feetech-FITEC-FS6535M-30kg-High-Torque_60200752064.html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

#### Quick Details

    Style:                    Radio Control Toy
    Power:                    Battery
    Plastic Type:             ABS
    Radio Control S...:       RC Hobby
    Brand Name:               Feetech
    Control system:           Digital
    Mesurements:              65.8x30.4x57.6
    Bearing Type:             2BB
    Color:                    Black
    Gear Type:                Metal gear
    Type:                     Car, 30kg high torque servo
    Material:                 Plastic
    Scale:                    1:5
    Place of Origin:          Guangdong, China (Mainland)
    Model Number:             FS6535M
    Motor Type:               carbon
    Weight:                   199g
    Stall Torque:             27.5kg.cm/33kg.c(4.8v/6v)
    Connector Leng...:        30cm

#### Package & Delivery

    Packaging Details: 30kg high torque servo / gift packing in export cartons
    Delivery Time:     1 to 3 days

#### Product Description

**Feetech/FITEC FS6535M 30kg High Torque Digital Servo**

|Feetech |Meas. |Weight| |Speed |Stall Torque| |Operating|
|:---:|:---:|:----:|:----:|:---:|:---:|:---:|:---:|
| |LxWxH | | | | | | |
|Item No.|(mm) |g |oz |sec/60 |kg.cm |oz.in |Voltage  |
| ------ | ------------ | ---- | ---- | ------- | ---------- | ----------- | ------- |
|FS6535M |65.8x30.4x57.6|199 |7.03  |0.3(4.8v)|27(4.8V) |382.57 (4.8V)|4.8~6.0V |
| | | | |0.27(6v) |33(6V) |459.09 (6V)  | |

Direction :CCW

Operating Angle :180degree

Required Pulse :500us-2500us

Bearing Type :2BB

Gear Type :Metal

Motor Type :Carbon

Connector Wire Length :30 cm

<!--![Drawing of the motor.](res/10-drawing.png)-->

<!--![Extra parts supplied with motor.](res/10-motor-extras.jpg)-->

Side view of motor.

<!--![Packaging for motor.](res/10-packaging.jpg)-->

### Risks and Solutions

* ** --
  *Solution:*
* ** --
  *Solution:*
* ** --
  *Solution:*
* ** --
  *Solution:*
* ** --
  *Solution:*
* ** --
  *Solution:*
* ** --
  *Solution:*

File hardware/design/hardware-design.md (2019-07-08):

\newpage

# Introduction

This document is to document design decisions for the chassis, particularly
concerning itself with the relationship between limbs and the motor
connections. For this document we aim to predict issues and potentially reduce
workload by finding symmetry.

\newpage

# Diagram

The first diagram shows the positioning of the motors in the DarwinOp assembly
manual. Here we can see the 20 motors in their positions and rotations, along
with the horn attachments for each.

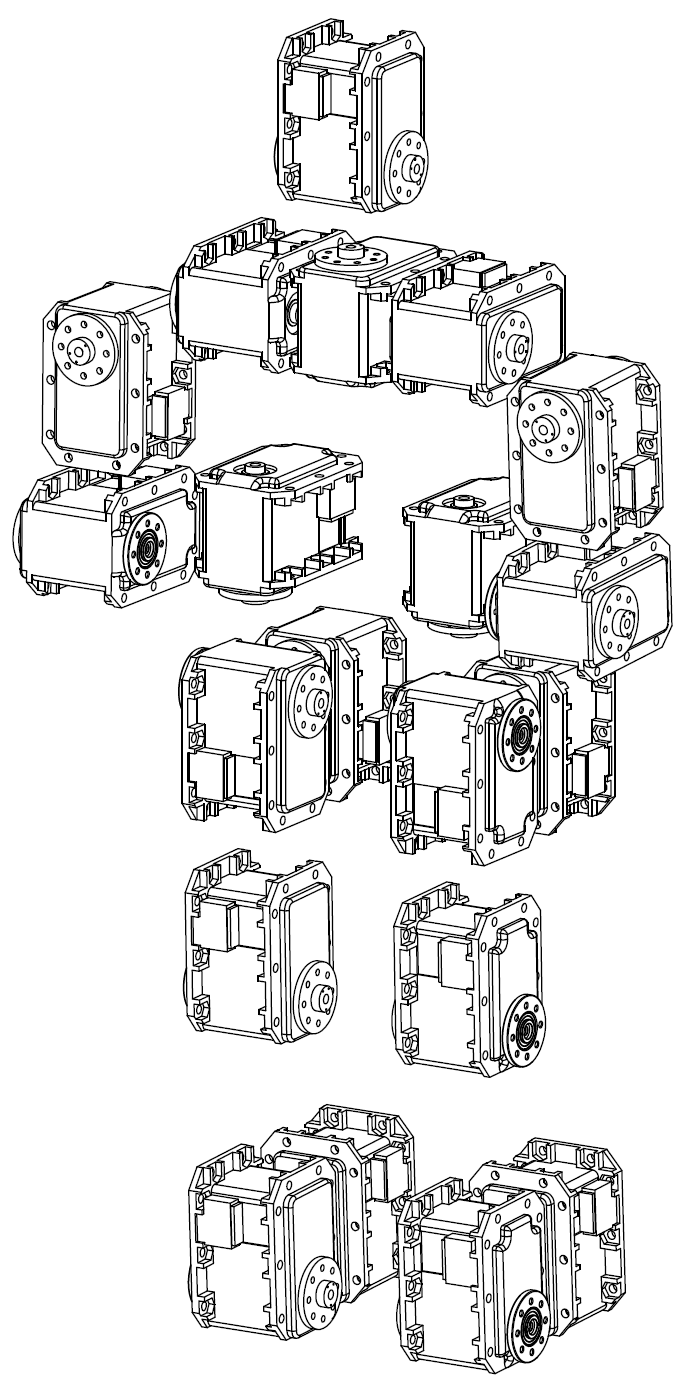
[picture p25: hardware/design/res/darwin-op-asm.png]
DARwin OP Assembly Manual by Robotis.


In the second diagram we see our similar recreation, showing labelled motors
and limbs which we will discuss in the *Breakdown* section.

Basic block diagram of our platform.

The parts are known as follows (modelled after humans):

* `[P0]` -- Head
* `[P1]` -- Torso
* `[P2]` -- Left upper arm
* `[P3]` -- Right upper arm
* `[P4]` -- Left lower arm
* `[P5]` -- Right lower arm
* `[P6]` -- Left thigh
* `[P7]` -- Right thigh
* `[P8]` -- Left shin
* `[P9]` -- Right shin
* `[P10]` -- Left foot
* `[P11]` -- Right foot

\newpage

# Breakdown

Parts with left and right symmetry have been grouped, with the additional
grouping as follows:

* `[P6]`, `[P7]`, `[P8]` and `[P9]` are essentially the same with identical
connecting parts each side.
* `[P4]` and `[P5]` are the same as `[P6]`, `[P7]`, `[P8]` and `[P9]`, but with
no end connector.

Essentially this means that we have a total of 4 unique parts.

## `[P0]` Head

**TODO:** Write this section.

## `[P1]` Torso

**TODO:** Write this section.

## `[P2]` Left Upper Arm & `[P3]` Right Upper Arm

**TODO:** Write this section.

## `[P4]` Left Lower Arm & `[P5]` Right Lower Arm

**TODO:** Write this section.

## `[P6]` Left Thigh & `[P7]` Right Thigh

**TODO:** Write this section.

## `[P8]` Left Shin & `[P9]` Right Shin

**TODO:** Write this section.

## `[P10]` Left Foot & `[P11]` Right Foot

**TODO:** Write this section.

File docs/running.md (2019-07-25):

# Running

To run, simply push to the target device (e.g. `scp`) and run:

    ./robot

You will need to make sure that you copy all relevant configuration files,
libraries, scripts, etc. If in doubt, copy everything!

## Additional Information

* [Command Line](../source/doc/command-line.md) - Command line arguments to
directly control motors.
* [Compiling](source/doc/compile.md) - Additional information on compiling the
code.
* [SM30 Protocol](../source/doc/protocol-handout.txt) - (Translated) Communication
protocol.
* [SM30 Bus](../source/doc/serial-bus-intelligent-servo.txt) - (Translated) Motor
table control.
* [SM30 Defaults](../source/doc/sm30-default-values.md) - Data pulled from factory
motors.

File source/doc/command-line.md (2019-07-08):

# Command Line

## Help

To display the help, simply run `-h` or `--help`.

**Note** that when this is run, the main program will not be run. This is a
feature intended to allow you to read the help message without program related
print data hiding it.

## Motor

This command line option is activated by running `-m` or `--motor`. Information
can be viewed by observing the *help* argument. The following is to help you do
some basic debug work on the motors.

### Motor Status

The most basic command to get working is the "ping" command. This allows you to
do the following:

* Confirm the serial communications are correct, i.e. the baud rate, check
bits, bytes conversion, etc.
* Confirm the motors is correctly connected.

To perform this, run the following:

    ./robot FE 0 01 1

Breaking this down, `FE` is the broadcast motor ID and all motors will respond.
After this, `0` is the number of parameters (i.e. the payload), `01` is the
command byte for ping and `1` indicates that we are waiting for a response from
the motor.

**Note** that if more than one motor is attached, they will all respond. The
broadcast address `FE` should be used carefully.

All going well, the motor should respond with:

* Motor ID: The ID of the motor, by default `01`.
* Number of parameters: This should be `0`.
* Working status (command): If all is good, the motor will return `00`.

### Additional Information

For more information please see the [Protocol Manual](doc/protocol-handout.txt)
and the [Memory Table](doc/serial-bus-intelligent-servo.txt).

Some additional details that the manual doesn't mention:

* The default baud rate of a factory made motor is actually 115200 bits per
second.
* Many of the default values are completely different from what they document,
see our manual recording of [factory values](doc/sm30-default-values.md).

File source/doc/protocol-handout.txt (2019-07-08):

Serial bus intelligent servo
SMS1.0 Protocol Manual
revise history
date        version     update content      Formulator
2017.03.01  V1.00       Initial formulation Alex lee

1.0 Communication Protocol Summary

  The SMS1.0 protocol is primarily applicable to the FEETECH SMS series of servo. The SMS series servos are based on ARM 32-bit microcontrollers with
main control core, position sensing adopts 360 degree 12-bit precision magnet sensing angle scheme, and communication level is stronger
RS485 mode of anti-interference ability.

  The controller and the servo communicate in a question and answer manner, the controller issues an instruction packet, and the servo returns a response packet.

  Multiple servos are allowed in a bus control network, so each servo is assigned a unique ID number within the network.
The control command issued by the controller contains the ID information, and only the servo that matches the ID number can receive the command completely, and
Returns a response message.

  The communication mode is serial asynchronous mode. One frame of data is divided into 1 start bit, 8 data bits and 1 stop bit.
Even parity bit, a total of 10 bits.

1.1 instruction package

Instruction package format:

Header: Two 0XFFs are received consecutively, indicating that a packet has arrived.

ID number: Each servo has an ID number. The ID number ranges from 0 to 253 and is converted to hexadecimal 0X00 to 0XFD.

Broadcast ID: ID number 254 is the broadcast ID. If the controller sends an ID number of 254 (0XFE), all servos are received the commands, except for the PING command, do not return a response message (multiple servos are connected to the bus and cannot use the broadcast PING)

Data length: equal to the length of the parameter to be sent N plus 2, which is "N+2".

Instruction: Packet operation function code, see 1.3 Instruction Type for details.

Parameters: In addition to the instruction, additional control information is required. The max parameter supports a double-byte parameter to represent a memory value. The section order refers to the servo manual of the servo manual (the order of the servos of different models is different).

Checksum: Checksum, Sum, calculated as follows

Check Sum = ~ (ID + Length + Instruction + Parameter1 + ... Parameter N)
If the calculation in parentheses exceeds 255, the lowest byte is taken, and "~" indicates negation.

1.2 Response package

The response packet is the response of the servo to the controller. The response packet format is as follows:

    The returned response packet contains the current state of the servo ERROR. If the current working state of the servo is not normal,
The section is reflected by this bit(see the manual memory control table for the meaning of each state). If ERROR is 0, the servo has no error message.

    If the instruction is a read command (READ DATA), then Parameter1 ...Parameter N is the read information.

1.3 Instruction type

The instructions available for the SMS 1.0 protocol are as follows:

instruction     Features        value       Parameter length
PING (query)    Query work status    0x01    0
READ DATA (read) Query the characters in the control table 0x02 2
WRITE DATA (write) Write characters to the control table 0x03 Greater than or equal to 1
REGWRITE DATA (asynchronous write) Similar to WRITE DATA, but the control characters are not take action immediately after written ,until the ACTION command arrives  0x04  Not less than 2
ACTION (execute asynchronous write)  Trigger REG WRITE write action  0x05  0
SYCNWRITE DATA   using in simultaneous control of multiple servos  0x83  Not less than 2
RESET (reset)  Reset the control table to the factory value  0x06  0

1.3.1 Query Status Command PING

Features        Read the working state of the servo
length      0X02
instruction     0X01
parameter       no

The PING command uses the broadcast address and the servo also returns a response message.

Example 1 Read the working status of the servo with ID number 1
Instruction frame: FF FF 01 02 01 FB ` (sent in hexadecimal)
Header      ID      Effective data length       instruction     Checksum
0XFF 0XFF   0X01    0X02                        0X01            0XFB
Returned data frame: FF FF 01 02 00 FC (hexadecimal display)
Header      ID      Effective data length       Working status      Checksum
0XFF 0XFF   0X01    0X02                        0X00                0XFC

1.3.2 Read Instruction READ DATA
Features    Read data from the servo memory control table
length      0X04
instruction 0X02
Parameter 1 The first address of the data readout segment
Parameter 2 Read data length

Example 2 Read the current position of the servo with ID 1 (low byte first, high byte last).
    Two bytes are read from the address 0X38 in the control table .
    Instruction frame: FF FF 01 04 02 38 02 BE (sent in hex)
Header      ID      Effective data length       instruction     parameter       Checksum
0XFF 0XFF   0X01    0X04                        0X02            0X38 0X02       0XBE

    Returned data frame: FF FF 01 04 00 18 05 DD (hexadecimal display)
Header      ID      Effective data length       Working status      parameter       Checksum
0XFF 0XFF   0X01    0X04                        0X00                0X18 0X05       0XDD
    Read two bytes of data are: low byte L 0X18 high byte H 0X05
    Two-byte synthesis 16-bit data 0X0518 , in decimal, the current position is 1304.

1.3.3 Write WRITE DATA
Features        Write data to the servo memory control table
length          N+3 (N is the parameter length)
instruction     0X03
Parameter 1     The first address of the data write segment
Parameter 2     The first data written
Parameter 3     The Second data
Parameter N+1   TheNth data

Example 3 sets an arbitrary numbered ID to 1.
    The address where the ID number is stored in the control table is 5, so write 1 at address 5. Send the ID of the instruction package using
broadcast ID (0xFE).
Instruction frame: FF FF FE 04 03 05 01 F4 (sent in hexadecimal)
Header      ID      Effective data length       instruction     parameter       Checksum
0XFF 0XFF   0XFE    0X04                        0X03            0X05 0X01       0XF4
    Since the instruction is sent with the broadcast ID, no data is returned.
    In addition, the memory table EPROM has a protection lock switch. It needs to be turned off before modifying the ID. Otherwise, the example ID number will not be saved when power down.
For detailed operation, please refer to the memory table or operation manual of the specific servo model.

Example 4 Controls the ID1 servo to rotate to a position of 2048 at 1000 rpm.

    The first address of the target position in the control table is 0X2A , so the writing of six consecutive bytes of data starts at address 0X2A.
They are position data 0X0800 (2048); time data 0X0000 (0); speed data 0X03E8 (1000).
The ID that sending instruction packet uses a non-broadcast ID (0xFE), so the servo will return a status packet when the command is received.

Command frame: FF FF 01 09 03 2A 00 08 00 00 E8 03 D5 (send in hexadecimal)
Header      ID          Effective data length           instruction         parameter           Checksum
0XFF 0XFF   0X01        0X09                            0X03                0X2A                0XD5
                                                                            0X00 0X08
                                                                            0X00 0X00
                                                                            0XE8 0X03

Returned data frame: FF FF 01 02 00 FC (hexadecimal display)
Header      ID      Effective data length       Working status      Checksum
0XFF 0XFF   0X01    0X02                        0X00                0XFC
Returning to the working state is 0, indicating that the servo has received the command correctly and error-free and has started execution.

1.3.4 Asynchronous Write Command REG WRITE

    The REG WRITE instruction is similar to WRITE DATA except that the execution time is different. When receiving a REG WRITE command frame,
Store the received data in a buffer spare and set the Registered Instruction register to 1. After receiving ACTION instruction, the stored instructions are finally executed.

Length          N+3 (N is the number of data to be written)
Instruction     0X04
Parameter 1     data to be written to the first address of the area
Parameter 2     The first data to be written
Parameter 3     The second data to be written
Parameter N+1   The Nth data to be written

Example 5 Control ID1 to ID10 servos rotate to a position of 2048 at 1000 rpm, only the ID in the following command package which
on the bus and receiving the instruction and returning, the other ID numbers are not returned on the bus.
ID 1    asynchronous write command packet: FF FF 01 09 04 2A 00 08 00 00 E8 03 D4
ID 1                       return package: FF FF 01 02 00 FC
ID 2   asynchronous write command package: FF FF 02 09 04 2A 00 08 00 00 E8 03 D3
ID 3   asynchronous write command package: FF FF 03 09 04 2A 00 08 00 00 E8 03 D2
ID 4  Asynchronous Write Instruction Pack: FF FF 04 09 04 2A 00 08 00 00 E8 03 D1
ID 5    asynchronous write command packet: FF FF 05 09 04 2A 00 08 00 00 E8 03 D0
ID 6   asynchronous write command package: FF FF 06 09 04 2A 00 08 00 00 E8 03 CF
ID 7    asynchronous write command packet: FF FF 07 09 04 2A 00 08 00 00 E8 03 CE
ID 8    Asynchronous Write Command Packet: FF FF 08 09 04 2A 00 08 00 00 E8 03 CD
ID 9   asynchronous write command package: FF FF 09 09 04 2A 00 08 00 00 E8 03 CC
ID10 asynchronous write instruction package: FF FF 0A 09 04 2A 00 08 00 00 E8 03 CB

1.3.5 Execute asynchronous write command ACTION

Features        Trigger REG WRITE instruction
length          0X02
instruction     0X05
parameter       no

    The ACTION command is very useful when controlling multiple servos at the same time.
    When controlling multiple servos, use the ACTION command to have the first and last servos perform their own movements simultaneously.
There is no delay in the middle.
    When sending an ACTION command to multiple servos, the broadcast ID (0xFE) is used, so there is no data frame returned after sending this command.

Example 6 After controlling the ID1 to ID10 servos to rotate at a speed of 1000 rpm to 2048 with asynchronous write command sending out.
To execute an asynchronous write instruction, the following instruction packet ( FF FF FE 02 05 FA ) needs to be sent .
All the servos on the bus will run the previously received asynchronous write instruction after receipt of this instruction.

1.4.5 Synchronous Write Command SYNC WRITE
Features        Used to control multiple servos at the same time.
ID              0XFE
length          (L + 1) * N + 4 (L: data length sent to each servo, N: number of servos)
instruction     0X83
Parameter 1     writes the first address of the data
parameter 2     The length of the data written(L)
Parameter 3     ID number of the first servo
Parameter 4     written to the first data of the first servo
Parameter 5     written to the second data of the first servo
...
Parameter L+3   written to the Lth data of the first servo
Parameter L+4   ID number of the second servo
Parameter L+5   written to the first data of the second servo
Parameter L+6   written to the second data of the second servo
...
Parameter 2L+4 is written to the Lth data of the second servo
...
    Unlike the REG WRITE+ACTION instruction, this command's real-time performance is higher than it, and a SYNC WRITE instruction can be modified the contents of the control table of multiple servos at one time, but the REG WRITE+ACTION instruction is done step by step. 
Otherwise, use SYNC WRITE instruction, the length of the written data and the first address of the saved data must be the same.

Example 7 For ID1-ID4 A total of 4 servos first address 0X2A write position 0X0800 time 0X0000 and speed 0X03E8 
( low bit is in the front and the high bit is in the back ).

Command frame: FF FF FE 20 83 2A 06 01 00 08 00 00 E8 03 02 00 08 00 00 E8 03 03 00 08
00 00 E8 03 04 00 08 00 00 E8 03 58 (sent in hex)
Header      ID      Effective data length       instruction     parameter                               Checksum
0XFF 0XFF   0XFE    0X20                        0X83 OX2A OX06                                          0X58
                                                                OX01 OX00 OX08 OX00 OX00 OXE8 OX03
                                                                OX02 OX00 OX08 OX00 OX00 OXE8 OX03
                                                                OX03 OX00 OX08 OX00 OX00 OXE8 OX03
                                                                OX04 OX00 OX08 OX00 OX00 OXE8 OX03

Since the instruction is sent with the broadcast ID, no data is returned.

1.4.6 Reset Instruction RESET
Features        Reset specific data in the memory control table (specific servo models are used)
length          0X02
instruction     0X06
parameter       no

Example, reset the servo, the ID number is 0.

Instruction frame: FF FF 01 02 06 F6 (sent in hexadecimal)
Header      ID      Effective data length       instruction     Checksum
0XFF 0XFF   0X00    0X02                        0X06            0XF7

Returned data frame: FF FF 01 02 00 FC (hexadecimal display)
Header      ID      Effective data length       Working status      Checksum
0XFF 0XFF   0X01    0X02                        0X00                0XFC

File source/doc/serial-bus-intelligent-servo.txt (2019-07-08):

Serial bus intelligent servo
SMS1.0 memory table
revise history
date		    version     update content
2016.12.21      V1.00       Initial formulation
2017.3.7        V1.01       1, modify the document format
                            2, increase overcurrent protection
                            3, increase mode 2 function
                            4, modify the 1.3 chapter error
                            5. Add 1.4 chapters
2017.7.20       V1.02       Fix mistakes

1.1 ERROR Current status

    The returned response packet contains the current ERROR status of the servo. If the current working status of the servo is not normal,
It will be reflected by this byte. The information of each representative is as follows:
BIT     name                            detailed
BIT7    0                               ---
BIT6    0                               ---
BIT5    overload                        Output torque is less than the load set
BIT4    0                               ---
BIT3    Overcurrent                     Current exceeds the specified range.
BIT2    overheat                        Temperature exceeds the specified range.
BIT1    Angle error                     Angle sensor error set
BIT0    Overvoltage and undervoltage    The voltage is set to exceed the specified range.
    If ERROR is 0, the servo has no error message.

1.2 memory control table

    The information and control parameters of the robot servo itself form a table that is stored in its RAM and EEPROM areas on control chip.
. We can achieve real-time control of the servo by modifying the contents of the table in real time.
This table is called the memory control table and looks like this:

address     Command item        Read and write      Initial value       Storage area
0 (0x00)    --                  --                  --                  EEPROM
1 (0x01)    --                  --                  --
2 (0x02)    --                  --                  --
3 (0x03)    Software version(L)    read             --
4 (0x02)    Software version(H)    read             --
5 (0x05)    ID                  Read/write          00 (0x00)
6 (0x06)    Baud rate           Read/write          00 (0x00)
7 (0x07)    Return delay time   Read/write          00 (0x00)
8 (0x08)    Response status level   Read/write      01 (0x01)
9 (0x09)    Minimum angle limit (L) read/write      00 (0x00)
10 (0x0A)   Minimum angle limit (H) read/write      00 (0x00)
11 (0x0B)   Maximum angle limit (L) read/write      15 (0x0F)
12 (0x0C)   Maximum angle limit (H) read/write      255 (0xFF)
13(0x0D)    Maximum temperature limit   Read/write  80 (0x50)
14 (0x0E)   Maximum input voltage   Read/write      140 (0xFA)
15 (0x0F)   Minimum input voltage   Read/write      60 (0x32)
16 (0x10)   Maximum torque (L)      Read/write      03(0x03)
17 (0x11)   Maximum torque (H)      Read/write      232 (0xE8)
18 (0x12)   --                    --                --
19 (0x13)   Unloading condition     Read/write      47 (0x2F)
20 (0x14)   LED alarm condition     Read/write      47 (0x2F)
21 (0x15)   P                       Read/write      15 (0x0F)
22 (0x16)   D                       Read/write      00 (0x00)
23 (0x17)   I                       Read/write      00 (0x00)
24 (0x18)   Minimum PWM (L)         Read/write      100 (0x64)
25 (0x19)   Minimum PWM (H)         Read/write      100 (0x64)
26 (0x1A)   Clockwise insensitive zone  Read/write  01 (0x01)
27(0x1B)    Counterclockwise insensitive zone   Read/write  01 (0x01)
28 (0x1C)   Integration limit (L)   Read/write      00 (0x00)
29 (0x1D)   Integration limit (H)   Read/write  00 (0x00)
30 (0x1E)   --                       --                 --
31 (0x1F)   --                       --                 --
32 (0x20)   --                      --                  --
33 (0x21)   Position correction (L) Read/write          00 (0x00)
34 (0x22)   Position correction (H) Read/write          00 (0x00)
35 (0x23)   Operating mode          Read/write          00 (0x00)
36 (0x24)   Protection current (L)  Read/write          07(0x07)
37 (0x25)   --                      --                  --
38 (0x26)   --                      --                  --
39 (0x27)   --                      --                  --
40 (0x28)   Torque switch       Read/write              00 (0x00)               RAM
41 (0x29)   --                  --                      --
42 (0x2A)   Target position (L) Read/write              --
43 (0x2B)   Target position (H) Read/write              --
44 (0x2C)   Running time (L)    Read/write              00 (0x00)
45 (0x2D)   Running time (H)    Read/write              00 (0x00)
46 (0x2E)   Running speed (L)   Read/write              00 (0x00)
47 (0x2F)   Running speed (H)   Read/write              00 (0x00)
48 (0x30)   Lock sign           Read/write              00 (0x00)
49--55      --                  --                      --
56 (0x38)   Current position (L)    read                ?
57 (0x39)   Current position (H)    read                ?
58 (0x3A)   Current speed (L)       read                ?
59 (0x3B)   Current speed (H)       read                ?
60 (0x3C)   Current load (L)        read                ?
61 (0x3D)   Current load (H)        read                ?
62 (0x3E)   Current voltage         read                ?
63 (0x3F)   Current Temperature     read                ?
64 (0x40)   REG WRITE logo          read                00 (0x00)
65 (0x41)   --                      --                  --
66 (0x42)   Mobile sign             read                ?
67 (0x43)   Current target position (L) read            ?
68 (0x44)   Current target position (H) read            ?
69 (0x45)   Current current (L)         read            ?
70 (0x46)   Current current (H)         read            ?

    If the control parameter has the command of "L" and "H", the range is 0x00-0x3FF; the parameter only accounts for
a one-byte command with a range of 0x00—0xFE.
    The parameters saved in the RAM will not be saved after power-off,  the parameters stored in the EEPROM will be saved after power-off.
" -- " means that the parameters cannot be modified.
    The detailed description is as follows:

0x06 : baud rate
The address 0x06 defaults to 0, indicating a baud rate of 1M. You can modify the baud rate to the user's needs.
For other baud rates, the other baud rates will be restored to 1M. Pair of baud rate and corresponding calculation parameters
According to the following table:

Address 0x06    Hex     Actual baud rate    Target baud rate    error
0               0x00    1000000.0           1000000.0           0.000%
1               0x01    500000.0            500000.0            0.000%
2               0x02    250000.0            250000.0            0.000%
3               0x03    128000.0            128000.0            0.000%
4               0x04    115107.9            115200              0.079%
5               0x05    76923.0             76800               -0.160%
6               0x06    57553.9             57600               0.008%
7               0x07    38461.5             38400               -0.160%

0x07 : Return delay
    Set the return delay time, that is, how long the delay should be when the servo receives an instruction that needs to be answered
can be set by you. Time range: parameter (0~254)*2US, if parameter 250, that is, after 500us response;
The parameter is 0, which means the response is in the shortest time.

0x08 : response level
    Response level, set whether the servo returns data after receiving the data.
Address 0x08        returns the response packet
0                   Other than the read command and the PING command, the response packet is not returned.
1                   Return a response packet for all instructions

0x09 to 0x0C : angle limit
    Set the range of angle at which the servo can be operated. The minimum angle limit ≤ target angle value ≤ maximum angle limit value.
    Note that the minimum angle limit value must be less than the maximum angle limit value. If the target angle value exceeds the range, then equals to the limit value..

0x0D : maximum operating temperature
    Maximum operating temperature, if set to 80, the maximum temperature is 80 degrees and the setting accuracy is 1 degree.

0x0E : maximum working voltage
    The highest working voltage, such as high set to 85, the maximum working voltage is 8.5V, the setting accuracy is 0.1V

0x0F : minimum operating voltage
    The minimum working voltage, such as the high setting of 45, the minimum operating voltage is 4.5V, and the setting accuracy is 0.1V.

0x10 to 0x11 : output torque
    Set the maximum output torque of the servo. 1000 corresponds to the maximum output torque of the servo.

0x13/0x14 : Set the uninstall /LED alarm condition
BIT     Features
BIT7    --
BIT6    --
BIT5    If set to 1, reduce torque output / LED alarm when overload occurs
BIT4    --
BIT3    If set to 1, unloading torque/LED alarm when overcurrent occurs
BIT2    If set to 1, unloading torque/LED alarm when overheating occurs
BIT1    If set to 1, unload torque/LED alarm when the angle sensor is faulty
BIT0    If set to 1, unloading torque/LED alarm when voltage range is exceeded
    If the above occurs at the same time, follow the logic or principle, the LED alarm condition (0X14) is set to 0.
turn off LED, otherwise turn on the LED.

0x1A to 0x1B : dead zone
    The size of the dead zone of the position closed loop is set to 1 in both clockwise and counterclockwise directions. The dead zone is about 0.087 degrees.

0x21 to 0x22 : 0 point position correction
    0 point position correction, 0~2047 means positive direction, 2048~4095 means negative direction

0x23 : Run mode
    In the operation mode, the lower 4 bits take values (0~15) to set the operation mode, and the upper 4 bits to set the operation mode according to the bit value.
mode    Features
Mode 2  Set to 2, torque output mode, see section 2.4 for details.
Mode 1  Set to 1, motor speed mode, see section 2.3 for details.
Mode 0  Set to 0, servo control mode

0x24~0x25 : protection current
    When the current protection function is turned on (refer to 0x13/0x14 setting), the servo current is greater than the protection current,
Flow protection start, torque unload, servo status Error Current overload bit is set.
    After the current returns to normal, the write position update command can cancel the overcurrent protection.

0x28 : torque output switch
    Torque output switch: “1” on, “0” off.

0x2A ~ 0x2F : servo control
address     Features            Description
0x2A~0x2B   target location     The range is 0x0000—0x0FFF, and 0x0000 corresponds to 0 degrees, 0x0FFF corresponds to 360 degrees, deviation ± 0.4%
0x2C~0x2D   operation hours     The unit is: 1 millisecond, 0 corresponds to the maximum speed
0x2E~0x2F   Running speed       Priority > Run Time, unit: 0.087 (degrees / second), 0 maximum speed
    Servo control parameters, time and speed at which the servo is running to the target position, where the speed parameter is priority to the time parameter
simultaneously write time and speed parameters, speed parameters are selected as control parameters, time parameter units
is 1 (milliseconds), the speed parameter unit is 0.087 (degrees/second). For example, the speed is (1000*0.087) degrees/second.
When set to 0, it corresponds to the maximum speed of the servo.

0x30 : lock function bit
    Lock function bit. If this bit is set to 0 to turn off the lock protection, the modification about parameters of the EEPROM area can be saved when power off.
    Note that the lock function bit is set to 0, the servo write speed will be slower, and write operations to the EEPROM area parameters frequently can affect the life of the servo.

0x38~0x48 : Servo feedback information
address     Features            Description
0x38~0x39   current location    Reference target position
0x3A~0x3B   Current speed       The unit has the same running speed, and the highest position is directional position
0x3C~0x3D   Current load        Value 0~1000
0x3E        Current voltage     Accuracy is 0.1V
0x3F        Current Temperature Accuracy is 1 degree
0x40        REG WRITE logo      If there is a REG WRITE instruction waiting for execution
                                , it is displayed as 1.
                                It is displayed as 0 after the REGWRITE instruction is executed.
0x41        Error               Steering gear status, refer to chapter 1.1
0x42        Mobile sign         A movement flag of 1 indicates that the servo is running
                                , 0 means stop running
0x43~0x44   Current target position Reference target position
0x45~0x46   Current current     The highest position is the direction

1.3 motor speed control mode
    The SMS series robot servo can be switched to the motor speed control mode, which can be used on the executive agency such as rotation of wheels, tracks, etc.
    Set the running mode (x23) to 1, and then give a speed (0x2e~0x2f). The motor will run by motor speed control mode.
Speed has a size and direction control, as shown in the following table:
BIT     15      14~0
VALUE   0/1     SPEED VALUE

    Address 0x2e to 0x2f: BIT15 is the direction bit, which is 0 in the positive direction and 1 in the opposite direction.
    BIT0~BIT14 is the size, the speed unit is 0.087 (degrees/second). If the input speed value is 1000, the servo running speed is (1000*0.087) degrees/second.

1.4 Torque mode
    SMS series robot servos can be switched to torque output mode, using on the circle rotation executive agency such as wheels, tracks, etc.
    Set the running mode (0x23) to 0, and then give a time (0x2c ~ 0x2d), the servo will run with constant torque
Torque has a size and direction control, as shown in the following table:
BIT     10      9~0
VALUE   0/1     TIME VALUE
    Address 0x2c to 0x2d: BIT10 is the direction bit, which is 0 in the positive direction and 1 in the opposite direction. 
BIT0~BIT9 is the size, the input range is 0~1000, and the torque output accuracy is 0.1%.

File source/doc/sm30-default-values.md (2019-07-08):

# SM30 Default Values

The following are a capture of the default values of the SM30.

**NOTE:** This was recorded once for one motor - it's assumed that there is no
variance in these factory values.

|Values in EEPROM |Pos  |R/W|Default|Actual|
|:---:|:---:|:-:|:-----:|:----:|
|*Reserved* |0x00 | / | |0x06  |
|*Reserved* |0x01 | / | |0x01  |
|*Reserved* |0x02 | / | |0x00  |
|SW_VERSION_LOW = |0x03 |R/ | |0x01  |
|SW_VERSION_HIGH = |0x04 |R/ | |0x00  |
|ID = |0x05 |R/W|0 |0x01  |
|BAUD_RATE = |0x06 |R/W|0 |0x04  |
|RETURN_DELAY_TIME = |0x07 |R/W|0 |0x00  |
|RESPONSE_STATUS_LEVEL =  |0x08 |R/W|1 |0x01  |
|MIN_ANGLE_LIMIT_LOW = |0x09 |R/W|0 |0x00  |
|MIN_ANGLE_LIMIT_HIGH = |0x0A |R/W|0 |0x00  |
|MAX_ANGLE_LIMIT_LOW = |0x0B |R/W|15 |0xFF  |
|MAX_ANGLE_LIMIT_HIGH = |0x0C |R/W|255 |0x0F  |
|MAX_TEMPERATURE_LIMIT =  |0x0D |R/W|80 |0x50  |
|MAX_INPUT_VOLTAGE = |0x0E |R/W|140 |0x0A  |
|MIN_INPUT_VOLTAGE = |0x0F |R/W|60 |0x46  |
|MAX_TORQUE_LOW = |0x10 |R/W|3 |0xEA  |
|MAX_TORQUE_HIGH = |0x11 |R/W|232 |0x03  |
|*Reserved* |0x12 | / | |0x01  |
|UNLOADING_CONDITION = |0x13 |R/W|47 |0x25  |
|LED_ALARM_CONDITION = |0x14 |R/W|47 |0x25  |
|P = |0x15 |R/W|15 |0x0F  |
|D = |0x16 |R/W|0 |0x0F  |
|I = |0x17 |R/W|0 |0x00  |
|MIN_PWM_LOW = |0x18 |R/W|100 |0x5A  |
|MIN_PWM_HIGH = |0x19 |R/W|100 |0x00  |
|CLOCKWISE_NO_CARE = |0x1A |R/W|1 |0x02  |
|CNTR_CLOCKWISE_NO_CARE = |0x1B |R/W|1 |0x02  |
|INTEGRATION_LIMIT_LOW =  |0x1C |R/W|0 |0x00  |
|INTEGRATION_LIMIT_HIGH = |0x1D |R/W|0 |0x00  |
|*Reserved* |0x1E | / | |0x01  |
|*Reserved* |0x1F | / | |0x05  |
|*Reserved* |0x20 | / | |0x00  |
|POSITION_CORRECT_LOW = |0x21 |R/W|0 |0x00  |
|POSITION_CORRECT_HIGH =  |0x22 |R/W|0 |0x00  |
|OPERATING_MODE = |0x23 |R/W|0 |0x00  |
|PROTECTION_CURRENT_LOW = |0x24 |R/W|7 |0x20  |
|*Reserved* |0x25 | / | |0x03  |
|*Reserved* |0x26 | / | |0x00  |
|*Reserved* |0x27 | / | |0x00  |

|Values in RAM |Pos  |R/W|Default|Actual|
|:---:|:---:|:-:|:-----:|:----:|
|TORQUE_SWITCH_LOW = |0x28 |R/W|0 |0x00  |
|*Reserved* |0x29 | / | |0x00  |
|TARGET_POSITION_LOW = |0x2A |R/W| |0x00  |
|TARGET_POSITION_HIGH = |0x2B |R/W| |0x00  |
|RUNNING_TIME_LOW = |0x2C |R/W|0 |0x00  |
|RUNNING_TIME_HIGH = |0x2D |R/W|0 |0x00  |
|RUNNING_SPEED_LOW = |0x2E |R/W|0 |0x00  |
|RUNNING_SPEED_HIGH = |0x2F |R/W|0 |0x00  |
|LOCK_SIGN = |0x30 |R/W|0 |0x01  |
|*Reserved* |0x31 | / | |0x00  |
|*Reserved* |0x32 | / | |0x00  |
|*Reserved* |0x33 | / | |0x00  |
|*Reserved* |0x34 | / | |0x00  |
|*Reserved* |0x35 | / | |0x00  |
|*Reserved* |0x36 | / | |0x00  |
|*Reserved* |0x37 | / | |0x00  |
|CURRENT_POSITION_LOW = |0x38 |R/ | |0x2B  |
|CURRENT_POSITION_HIGH =  |0x39 |R/ | |0x07  |
|CURRENT_SPEED_LOW = |0x3A |R/ | |0x00  |
|CURRENT_SPEED_HIGH = |0x3B |R/ | |0x00  |
|CURRENT_LOAD_LOW = |0x3C |R/ | |0x00  |
|CURRENT_LOAD_HIGH = |0x3D |R/ | |0x00  |
|CURRENT_VOLTAGE = |0x3E |R/ | |0x7C  |
|CURRENT_TEMPERATURE = |0x3F |R/ | |0x1A  |
|REG_WRITE_LOGO = |0x40 |R/ |0 |0x00  |
|*Reserved* |0x41 | / | |0x00  |
|MOBILE_SIGN = |0x42 |R/ | |0x00  |
|CURRENT_TARGET_POS_LOW = |0x43 |R/ | |0x2B  |
|CURRENT_TARGET_POS_HIGH =|0x44 |R/ | |0x07  |
|CURRENT_CURRENT_LOW = |0x45 |R/ | |0x00  |
|CURRENT_CURRENT_HIGH = |0x46 |R/ | |0x00  |

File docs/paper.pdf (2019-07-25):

# Black Sheep: Low-Cost Open Source Humanoid Robotics Research Platform

Daniel Barry 2 Merel Keijsers 1 Munir Shah 4 Humayun Khan 1 Banon Hopman 3 Simon Hoermann 1 3

1 HITLab NZ 2 College of Engineering 3 School of Product Design 4 Stats NZ

University of Canterbury, Christchurch, New Zealand

Abstract—In this paper we present a low-cost entrylevel 3D printed humanoid robotics platform for the kid-sized league of the RoboCup competition. We open source the platform under an MIT license and discuss the performance of the platform in the RoboCup World Cup competition in Sydney, Australia (2019). We offer source files for the chassis structure, a custom electronics solution for power delivery, as well as source code for the platform. The results of our work show that a low-cost humanoid platform is achievable but more work is necessary to be competitive in the domain.

This project was funded by the University of Canterbury.¹

Introduction

Embodied cognition suggests that cognition is dependent on the agent’s body, meaning that the agent’s ability to act and sense are important for developing intelligent behaviour [1]. If we extend this to artificial intelligence (AI), it could be strongly suggested that the development of human-like intelligence requires the agent to have a human-like body. Humanoid robotics research is quite an active and exciting field for exploring human-like behaviours, especially as the cost of hardware decreases and computational power increases.

In 1997 the concept of RoboCup was proposed as a standard AI problem, requiring advancements in multiple disciplines to solve [2]. The overall goal of the competition is that in 2050, the best robots compete against the best human football players in the world - and the robots win [3]. In the humanoid league in 2019, open problems include: walking on uneven artificial grass, seeing objects in a natural light environment, localizing in a highly symmetrical environment and cooperative agent behaviours. For the goal of testing the advancements of humanoid robotics and human-like artificial intelligence, RoboCup offers a suitably difficult problem space that is yet to be completely solved after more than 20 years.

The team Electric Sheep was created in 2017 and secured funding in 2018, where the team was able to qualify for the RoboCup World Cup in 2019 [4]. Electric Sheep is

1Funding received from HITLab NZ, the College of Engineering and the School of Product Design.


Fig. 1. Robots playing a game in controlled lighting.

notable as the first major league competitor from New Zealand and is currently the only competitor from New Zealand actively competing. The ambitious goal of creating a platform completely from scratch was set to both meet the team’s low-budget and to show that it is still possible for new teams to enter the competition. In the following we will discuss existing approaches, our approach, the results of the our approach and future work.

Background

Many platforms suitable to the humanoid RoboCup domain exist. We will discuss a small selection that we considered whilst choosing whether to create a new platform. The Darwin OP3 platform, the 3rd version of the well tested Darwin OP series, costs $11k USD [5]. The Darwin OP3, whilst suitable for the competition, costs too much to purchase a full team. The next platform we considered was the Poppy Humanoid, which is an open source bio-inspired humanoid - but also costs a similar amount (due to an increased number of motors) [6]. Another consideration was the NimbRo-OP2 platform which both has a very pleasing design and is a well tested platform at the RoboCup competition [7]. Unfortunately it is both too large and too expensive to usable in a multi-agent team. Finally we considered the HamBot platform, again a platform that had visited RoboCup but unfortunately suffered some issues and was later abandoned [8].

The most expensive aspect of each of the platforms was the motors and all of them use some model of the Dynamixel series created by Robotis (as seen in the Darwin OP3). These motors are favoured for multiple reasons including: The ability to daisy chain power and communications via the RS-485 standard, their relatively high accuracy (4096 position encoding), their intelligent control and monitoring (e.g. temperature, angle, current, torque, voltage) and their ability to set PID values.

After reviewing the platforms, it was most obvious these motor characteristics were most desirable during walking, and not in the arms or head motors where little to no feedback is generally required. We therefore saw an opportunity to greatly reduce the cost of the platform by replacing upper body motors with cheaper, zero feedback motors. Because of the power of the motors we required, the size and shape of the lower-cost motors were greatly different, forcing us to re-think the kinematic structure of the robot. This in turn led to the decision to create a platform from scratch, as almost everything needed to be redesigned. When redesigning we decided to keep the degrees of the freedom the original Darwin OP platform had in order to ensure flexibility close to a well tested platform.

Methodology

The platform was designed and built in just two months before the qualification for RoboCup 2019 for Sydney, Australia [9]. Many revisions were made between the original qualification and the competition as a result of continuous testing and redesigns. In this section we will discuss the design and creation of the humanoid platform, specifically the electronics, chassis and software respectively.

Electronics

Our platform requires several high-current voltage conversions to ensure the relevant components are powered. Mainly we require 12V (smart motors), 5V (PWM motors) and 5V (controller boards). The reason for isolating the controllers supply and the motors supply at 5V is to ensure the voltage sensitive controller boards are always supplied with a clean 5V supply rail. Under high current draw, the voltage may drop as the DC step-down converter reaches saturation. Both of the DC step-downs are required to deliver 10A and the USB 5V is required to deliver 3A, so for a safe power margin the power PCB was required to handle 30A.

Where possible we used off-the-shelf components to reduce risk, such as the DC step-down converters and the USB 5V supply. Unfortunately there was no off-the-shelf solution


Fig. 2. Simplified input/output power diagram.

we were able to find that allowed for switching between DC 17V and battery 16.8V (4 cell LiPo). Additionally we wanted the power supply to switch to DC when DC is available otherwise battery, alarm if the voltage drops too in the battery, ability to switch the output on/off, high current replaceable fuse and multiple output wires. Given our relatively unique requirements, we decided to design our own power circuit solution.


Fig. 3. The simple power PCB circuit design.


Fig. 4. Testing the power PCB design.

Chassis

The platform’s chassis was designed in the parametric CAD software OpenSCAD to allow the team’s mostly software based expertise to create 3D parts [10]. The platform was then printed in 1.75mm black PLA filament, chosen for it’s reduced negative effects when breathed in and the PLA’s ability to absorb impacts.


Fig. 5. Designing the platform’s head in OpenSCAD.

Software

The software is custom and without a framework, simply for the fact that time was limited and we needed to be able to rapidly develop software around the evolving hardware. Despite this, the software has remained mostly modular and each component is relatively isolated. We will give an overview of the areas of interest:

Behaviour: This code is simple fall-through state logic, where state is recalculated per look based on entryconditions. There is shared behaviour (such as falling down or listening to the game controller) and individual player behaviour.

Config: Our configuration system uses an open source C++ JSON library, allowing for a JSON template to define several overriding layers of configuration [11]. Configurations can be updated either via disk or debug server, with values able to be pulled in real-time over multiple threads. Values are cached once loaded in order to reduce conversion overheads.

Hardware: This section acts as an abstraction layer between hardware and software, where each piece of hardware usually expects to be able to block on the calling thread during an update. For this reason updates are performed on a separate hardware thread.

Localization: This is the start of an IMU based implementation of localization that attempts to track orientation. There is currently no drift correction, this simply shows how a future implementation may use an IMU to help track the robot’s position.

Motion: Here we have a scheduler that balances between running motion scripts (a procedure of actions for the motors to be take) and Rhoban’s inverse kinematics walk engine [12]. Scripts can be stacked, walking is merged together and each can be gracefully stopped.

Network: We have simple implementations for both the game controller (referee) [13] and open team communication [14].
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

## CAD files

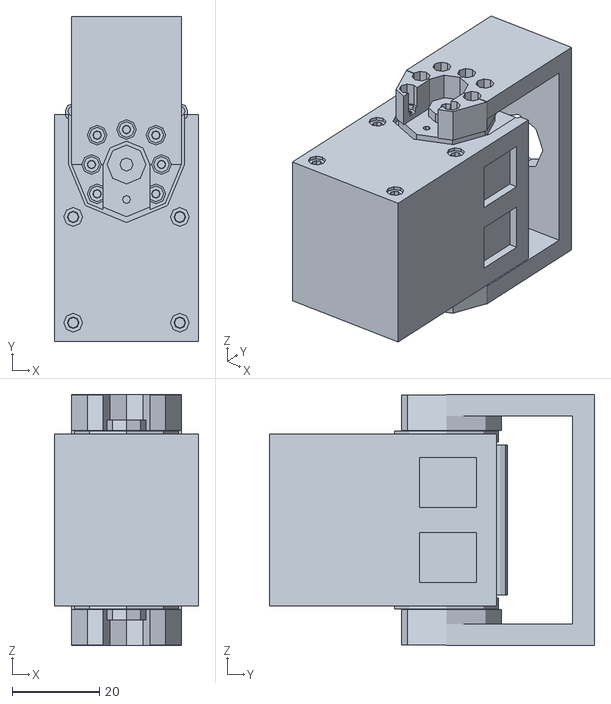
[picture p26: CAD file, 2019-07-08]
source/www/static/stl/motor-sm30-complete.scad.stl
33.0 x 74.4 x 57.5

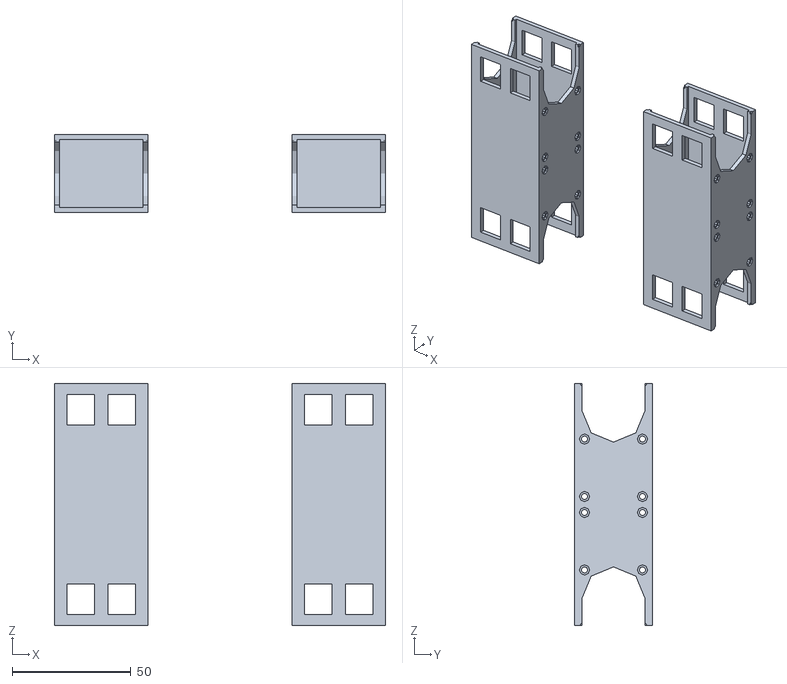
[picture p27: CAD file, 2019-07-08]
source/www/static/stl/thigh-complete.scad.stl
139.4 x 33.0 x 102.1

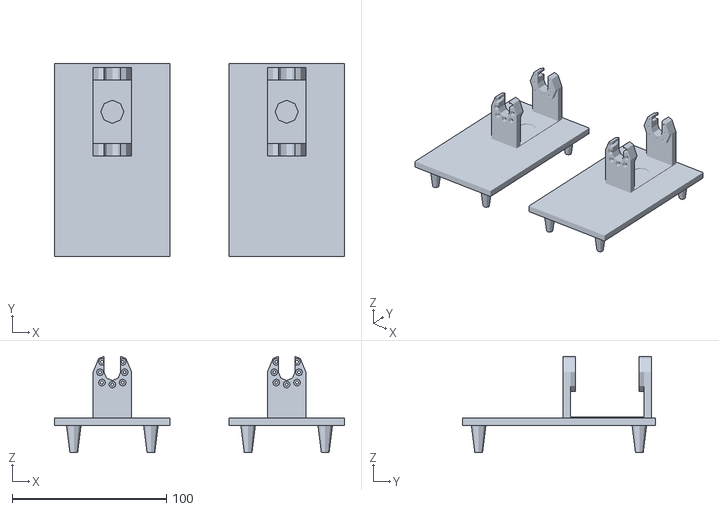
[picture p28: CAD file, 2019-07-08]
source/www/static/stl/foot-complete.scad.stl
188.0 x 125.0 x 62.5

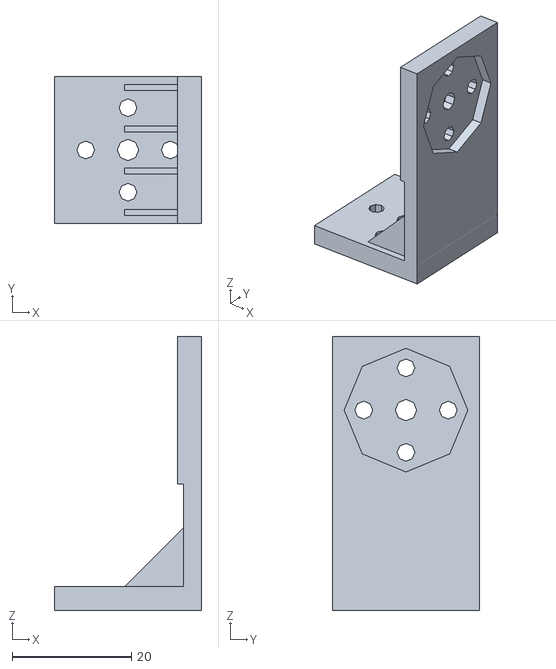
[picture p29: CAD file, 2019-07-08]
source/www/static/stl/neck-complete.scad.stl
24.7 x 24.8 x 46.0

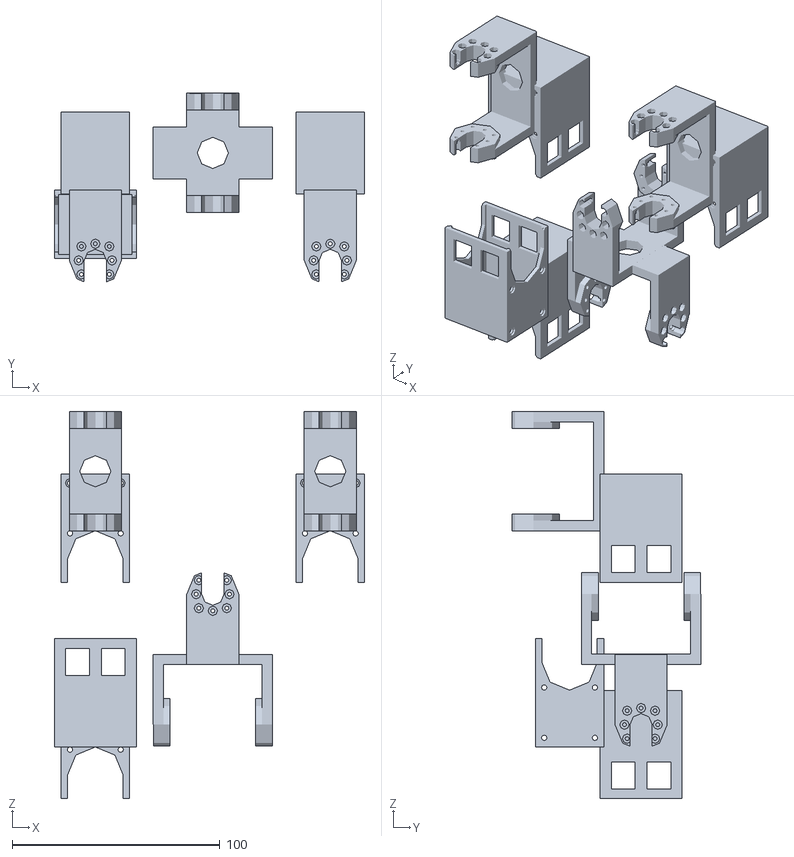
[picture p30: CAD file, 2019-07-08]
source/www/static/stl/hip-complete.scad.stl
149.2 x 90.8 x 186.1

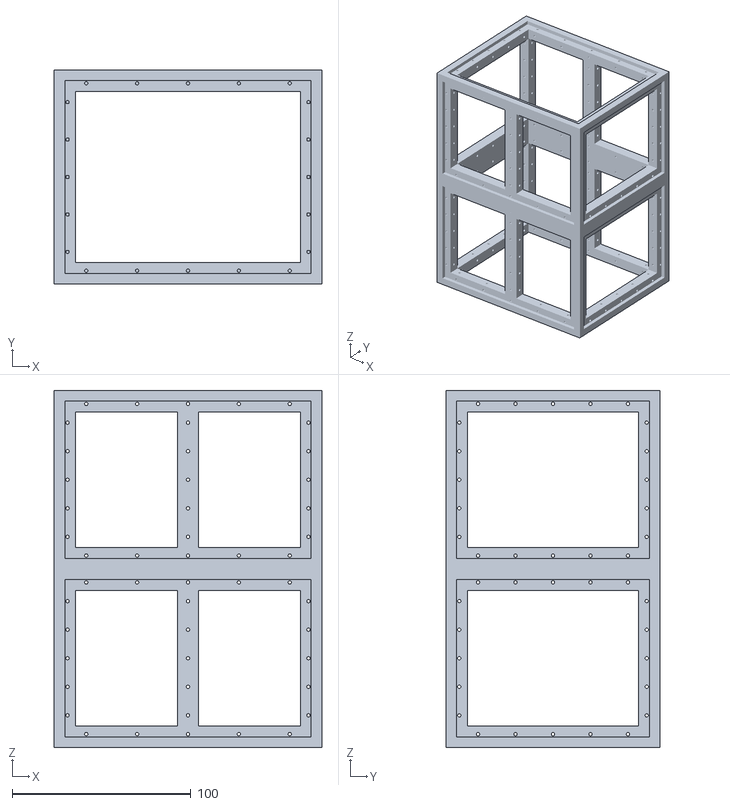
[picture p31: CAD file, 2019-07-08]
source/www/static/stl/torso-complete.scad.stl
150.0 x 120.0 x 200.0

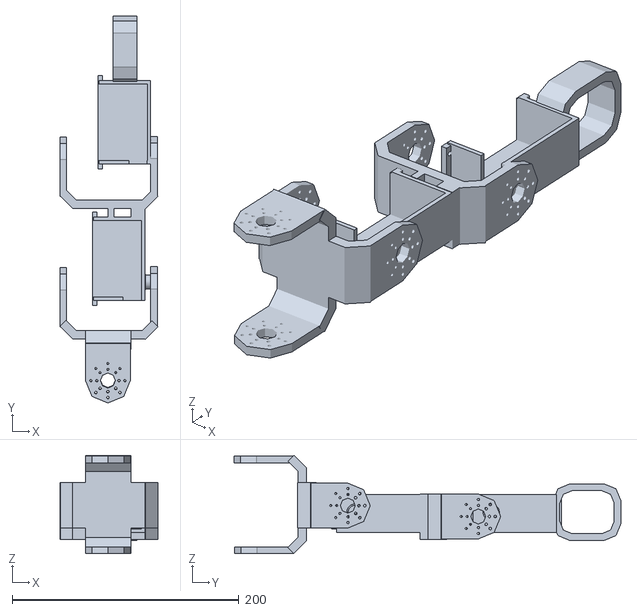
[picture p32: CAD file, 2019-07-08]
source/www/static/stl/complete-arm-right.scad.stl
86.6 x 341.1 x 86.6

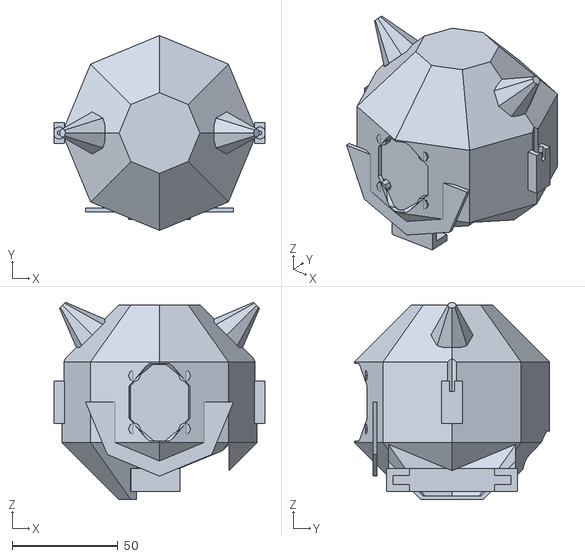
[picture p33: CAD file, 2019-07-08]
source/www/static/stl/head-complete.scad.stl
100.0 x 92.4 x 93.6

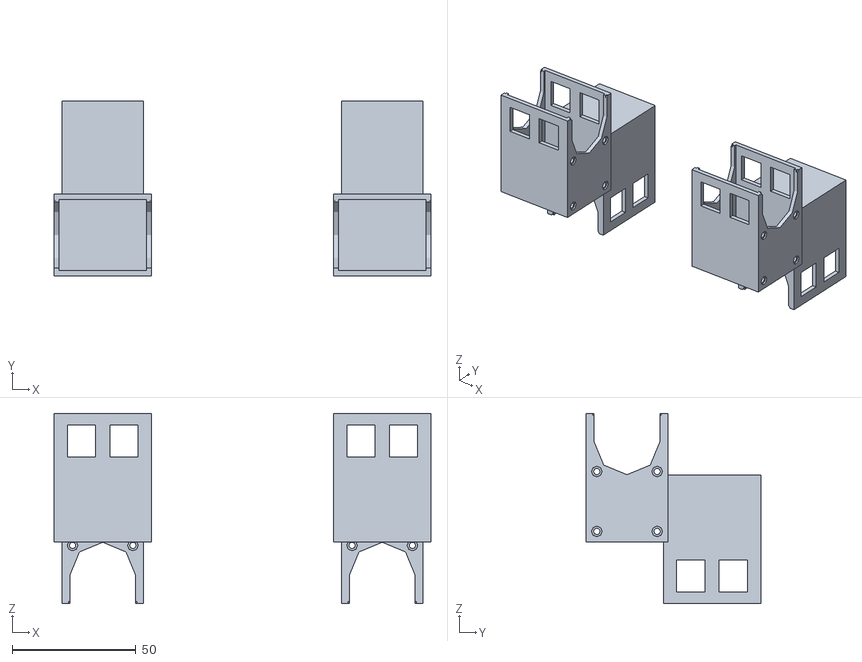
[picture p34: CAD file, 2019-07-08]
source/www/static/stl/ankle-complete.scad.stl
152.4 x 70.6 x 76.9

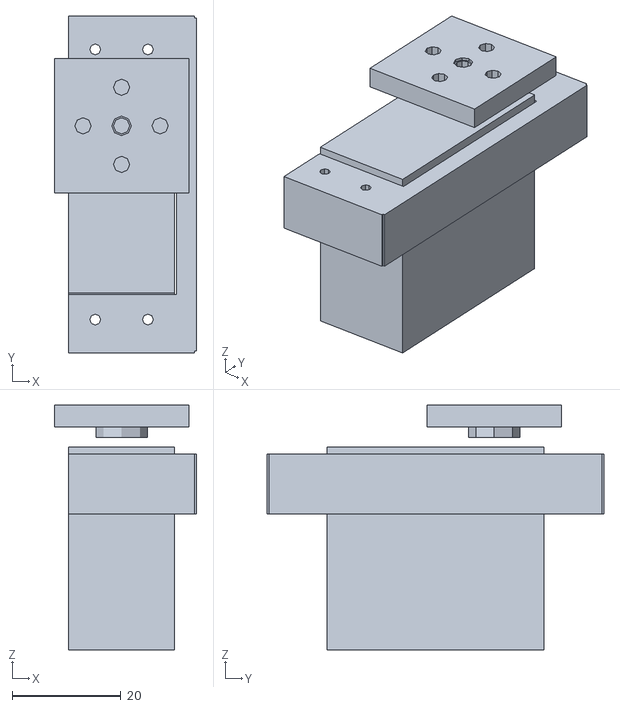
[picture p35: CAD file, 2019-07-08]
source/www/static/stl/motor-mg995-complete.scad.stl
26.2 x 62.1 x 45.1

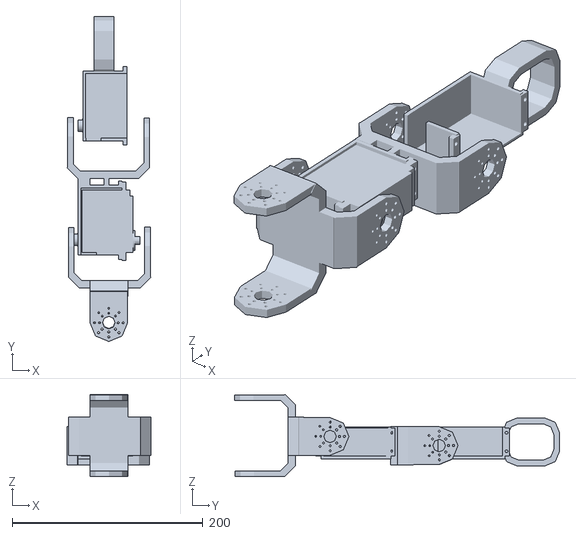
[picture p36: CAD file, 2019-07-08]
source/www/static/stl/complete-arm-left.scad.stl
88.1 x 341.1 x 86.6

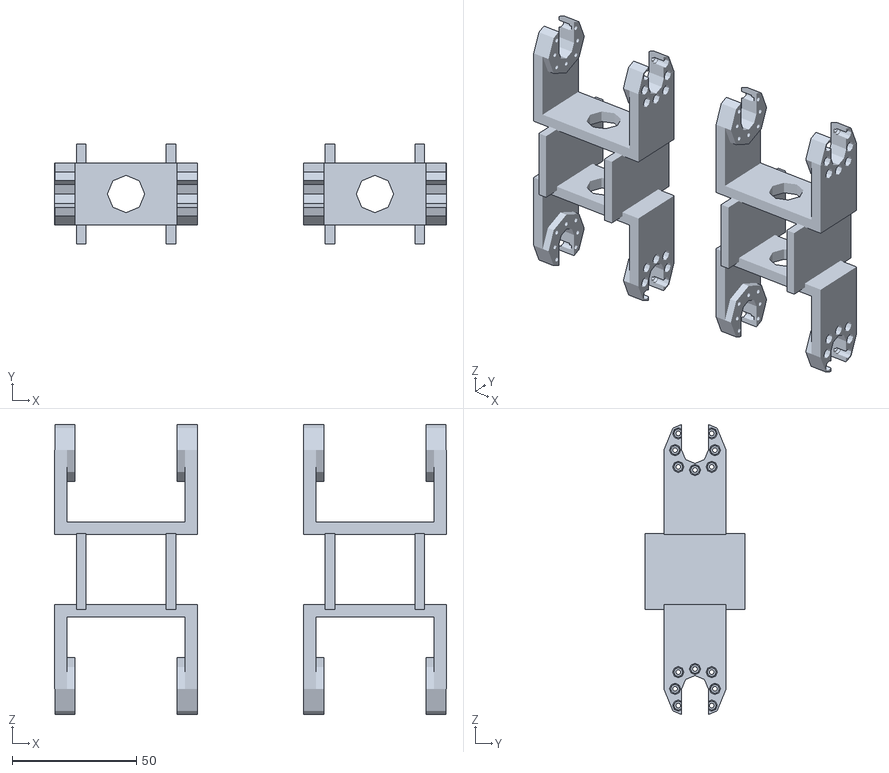
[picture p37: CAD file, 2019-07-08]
source/www/static/stl/shin-complete.scad.stl
157.5 x 40.0 x 116.6

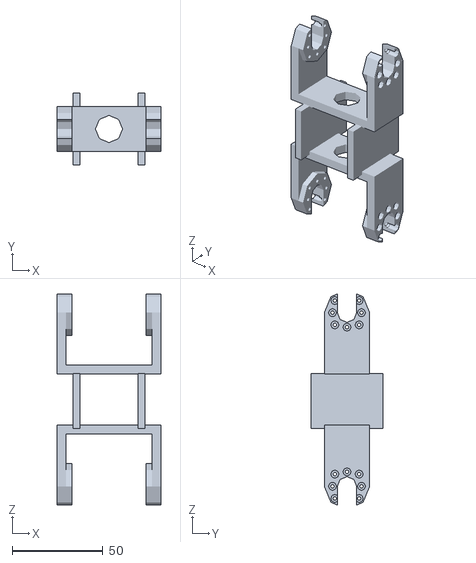
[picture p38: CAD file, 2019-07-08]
source/www/static/stl/shin-right.scad.stl
57.5 x 40.0 x 116.6

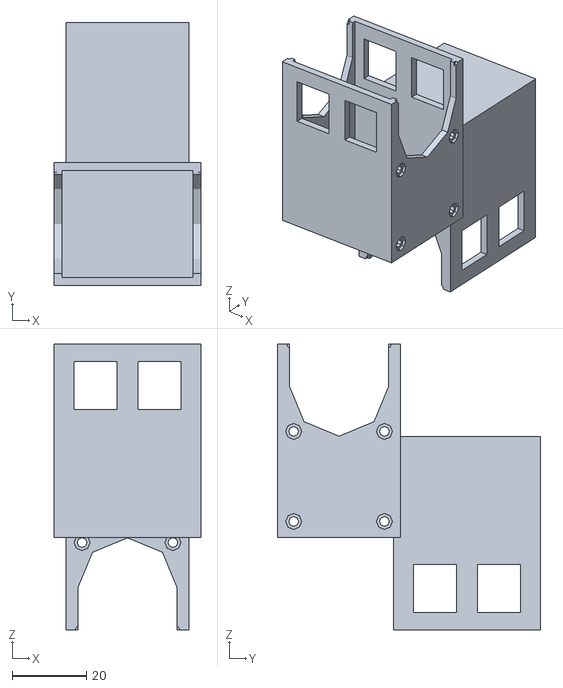
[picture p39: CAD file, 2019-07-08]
source/www/static/stl/hip-lower-right.scad.stl
39.4 x 70.6 x 76.9

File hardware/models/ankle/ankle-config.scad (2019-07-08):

/* "Resolution" of arcs */
if(str($qual) != "undef"){
  $fn = $qual;
}else{
  $fn = 64;
}
/* Constants in mm */
/* NOTE: None. */
/* Plastic colour */
PRINT_COLOR = [0.2, 0.2, 0.2];

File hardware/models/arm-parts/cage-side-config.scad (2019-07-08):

include <../Motor-FS6535/motor-fs6535-config.scad>
CAGE_SIDE_WALL_WIDTH=3;
CAGE_SIDE_BACKOFF=1;
CAGE_SIDE_HEIGHT=MOTOR_FS6535_BODY_HEIGHT-9;

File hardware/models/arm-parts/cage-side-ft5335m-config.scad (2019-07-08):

include <../Motor-FT5335M/motor-ft5335m-config.scad>
CAGE_SIDE_WALL_WIDTH=3;
//CAGE_SIDE_BACKOFF=1;
CAGE_SIDE_BACKOFF=0;
CAGE_SIDE_HEIGHT=MOTOR_FT5335M_CENTER_PLATE_OFFSET;

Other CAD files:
source/www/static/stl/motor-sm30-horn-mount-half.scad.stl
source/www/static/stl/armParts-left.scad.stl
source/www/static/stl/hip-upper-right.scad.stl
source/www/static/stl/motor-sm30-horn-bottom.scad.stl
hardware/models/arm-parts/upper-arm-config.scad
hardware/models/Motor-FS6535/motor-fs6535-config.scad
hardware/models/Motor-FS6535/motor-fs6535-horn-config.scad
hardware/models/Motor-FS6535/motor-fs6535-horn.scad
hardware/models/Motor-FS6535/motor-fs6535.scad
hardware/models/Motor-FT5335M/motor-ft5335M-config.scad
hardware/models/Motor-FT5335M/motor-ft5335M-horn-config.scad
hardware/models/Motor-FT5335M/motor-ft5335M-horn.scad
hardware/models/Motor-FT5335M/motor-ft5335M.scad
hardware/models/ankle/ankle-complete.scad
hardware/models/ankle/ankle-left.scad
hardware/models/ankle/ankle-right.scad
hardware/models/arm-parts/armParts-left-ft5335m.scad
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

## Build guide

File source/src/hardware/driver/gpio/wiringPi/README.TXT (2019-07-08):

wiringPi README
===============

Please note that the official way to get wiringPi is via git from
git.drogon.net and not GitHub.

ie.

  git clone git://git.drogon.net/wiringPi

The version of wiringPi held on GitHub by "Gadgetoid" is used to build the
wiringPython, Ruby, Perl, etc. wrappers for these other languages. This
version may lag the official Drogon release.  Pull requests may not be
accepted to Github....

Please see

  http://wiringpi.com/

for the official documentation, etc. and the best way to submit bug reports, etc.
is by sending an email to projects@drogon.net

Thanks!

  -Gordon

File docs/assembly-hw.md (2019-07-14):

# Assembly (Hardware)

**NOTE:** We will release assembly instructions if required, but recommend
waiting for the second version of the platform if possible. The 2nd version
will address:

* Reduce motor inaccuracies
* Approximately half the platform weight
* Increase strength of plastic to horn mounting
* Further platform advancements...

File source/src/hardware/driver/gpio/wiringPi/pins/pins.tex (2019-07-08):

\documentclass[12pt,a4paper]{article}
\parskip 1ex
\parindent 0em
\thispagestyle{empty}
\pagestyle{plain}
\pagenumbering{arabic}
\setlength{\topmargin}{0pt}
\setlength{\headheight}{0pt}
\setlength{\headsep}{0pt}
\setlength{\topskip}{0pt}
\setlength{\textheight}{240mm}
\setlength{\footskip}{5ex}
\setlength{\oddsidemargin}{0pt}
\setlength{\evensidemargin}{0pt}
\setlength{\textwidth}{160mm}
\usepackage[dvips]{graphics,color}
\usepackage{helvet}
\renewcommand{\familydefault}{\sfdefault}
\begin{document}
\begin{sffamily}
\definecolor{rtb-black}{rgb}  {0.0, 0.0, 0.0}
\definecolor{rtb-navy}{rgb}   {0.0, 0.0, 0.5}
\definecolor{rtb-green}{rgb}  {0.0, 0.5, 0.0}
\definecolor{rtb-teal}{rgb}   {0.0, 0.5, 0.5}
\definecolor{rtb-maroon}{rgb} {0.5, 0.0, 0.0}
\definecolor{rtb-purple}{rgb} {0.5, 0.0, 0.5}
\definecolor{rtb-olive}{rgb}  {0.5, 0.5, 0.0}
\definecolor{rtb-silver}{rgb} {0.7, 0.7, 0.7}
\definecolor{rtb-grey}{rgb}   {0.5, 0.5, 0.5}
\definecolor{rtb-blue}{rgb}   {0.0, 0.0, 1.0}
\definecolor{rtb-lime}{rgb}   {0.0, 1.0, 0.0}
\definecolor{rtb-aqua}{rgb}   {0.0, 1.0, 1.0}
\definecolor{rtb-red}{rgb}    {1.0, 0.0, 0.0}
\definecolor{rtb-fuchsia}{rgb}{1.0, 0.0, 1.0}
\definecolor{rtb-yellow}{rgb} {1.0, 1.0, 0.0}
\definecolor{rtb-white}{rgb}  {1.0, 1.0, 1.0}

\begin{center}
\bfseries{WiringPi: GPIO Pin Numbering Tables}\\
\tt{http://wiringpi.com/}
\end{center}

\begin{center}
\begin{tabular}{|c|c|c||p{8mm}|p{8mm}||c|c|c|c|}
\hline
\multicolumn{8}{|c|}{\bfseries{P1: The Main GPIO connector}}\\
\hline
\hline
WiringPi Pin	& BCM GPIO	& Name	& \multicolumn{2}{|c||}{Header}	& Name	& BCM GPIO	& WiringPi Pin\\
\hline
\hline
	& 			& \textcolor{rtb-red}{3.3v}	& \raggedleft{1} &  2 & \textcolor{rtb-maroon}{5v}	& 	& \\
\hline
8	& Rv1:0 - Rv2:2		& \textcolor{rtb-aqua}{SDA}	& \raggedleft{3} &  4 & \textcolor{rtb-maroon}{5v}	& 	& \\
\hline
9	& Rv1:1 - Rv2:3		& \textcolor{rtb-aqua}{SCL}	& \raggedleft{5} &  6 & \textcolor{rtb-black}{0v}	& 	& \\
\hline
7	& 4			& \textcolor{rtb-green}{GPIO7}	& \raggedleft{7} &  8 & \textcolor{rtb-yellow}{TxD}	& 14    & 15\\
\hline
	& 			& \textcolor{rtb-black}{0v}	& \raggedleft{9} & 10 & \textcolor{rtb-yellow}{RxD}	& 15	& 16\\
\hline
0	& 17			& \textcolor{rtb-green}{GPIO0}	& \raggedleft{11} & 12 & \textcolor{rtb-green}{GPIO1}	& 18	& 1\\
\hline
2	& Rv1:21 - Rv2:27	& \textcolor{rtb-green}{GPIO2}	& \raggedleft{13} & 14 & \textcolor{rtb-black}{0v}	& 	& \\
\hline
3	& 22			& \textcolor{rtb-green}{GPIO3}	& \raggedleft{15} & 16 & \textcolor{rtb-green}{GPIO4}	& 23	& 4\\
\hline
	& 			& \textcolor{rtb-red}{3.3v}	& \raggedleft{17} & 18 & \textcolor{rtb-green}{GPIO5}	& 24	& 5\\
\hline
12	& 10			& \textcolor{rtb-teal}{MOSI}	& \raggedleft{19} & 20 & \textcolor{rtb-black}{0v}	& 	& \\
\hline
13	& 9			& \textcolor{rtb-teal}{MISO}	& \raggedleft{21} & 22 & \textcolor{rtb-green}{GPIO6}	& 25	& 6\\
\hline
14	& 11			& \textcolor{rtb-teal}{SCLK}	& \raggedleft{23} & 24 & \textcolor{rtb-teal}{CE0}	& 8	& 10\\
\hline
	& 			& \textcolor{rtb-black}{0v}	& \raggedleft{25} & 26 & \textcolor{rtb-teal}{CE1}	& 7	& 11\\
\hline
\hline
WiringPi Pin	& BCM GPIO	& Name	& \multicolumn{2}{|c||}{Header}	& Name	& BCM GPIO	& WiringPi Pin\\
\hline
\end{tabular}
\end{center}

Note the differences between Revision 1 and Revision 2 Raspberry
Pi's. The Revision 2 is readily identifiable by the presence of the 2
mounting holes.

The revision 2 Raspberry Pi has an additional GPIO connector, P5, which is next to the main P1 GPIO
connector:

\begin{center}
\begin{tabular}{|c|c|c||p{8mm}|p{8mm}||c|c|c|c|}
\hline
\multicolumn{8}{|c|}{\bfseries{P5: Secondary GPIO connector (Rev. 2 Pi only)}}\\
\hline
\hline
WiringPi Pin	& BCM GPIO	& Name	& \multicolumn{2}{|c||}{Header}	& Name	& BCM GPIO	& WiringPi Pin\\
\hline
\hline
	& 		& \textcolor{rtb-maroon}{5v}	& \raggedleft{1} &  2 & \textcolor{rtb-red}{3.3v}	& 	&	\\
\hline
17	& 28		& \textcolor{rtb-green}{GPIO8}	& \raggedleft{3} &  4 & \textcolor{rtb-green}{GPIO9}	& 29	& 18	\\
\hline
19	& 30		& \textcolor{rtb-green}{GPIO10}	& \raggedleft{5} &  6 & \textcolor{rtb-green}{GPIO11}	& 31	& 20	\\
\hline
	& 		& \textcolor{rtb-black}{0v}	& \raggedleft{7} &  8 & \textcolor{rtb-black}{0v}	& 	&	\\
\hline
\hline
WiringPi Pin	& BCM GPIO	& Name	& \multicolumn{2}{|c||}{Header}	& Name	& BCM GPIO	& WiringPi Pin\\
\hline
\end{tabular}
\end{center}

\end{sffamily}
\end{document}

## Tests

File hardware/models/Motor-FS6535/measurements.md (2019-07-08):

# Diagram

        x ______ x
       / /\  __ \ \
    H / /  \(   \\ \
     / /    \\ __)\ \ D
    x /      \ ____\ \
      \       \\___\\ \
       \       \_____\ x
        \      /     / x
         \    /     / /
          \  /     / / W
           \/_____/ x

# Sizes

Accuracy to +/- `0.05cm`.

* Main box width = `1.95cm`
* Main box height = `3.80cm`
* Main box depth = `3.95cm`
* Main box height with horn = `4.70cm`
* Main box mounts screw to screw centroid width = `1.00cm`
* Main box mounts screw to screw centroid height = `2.85cm`
* Main box mounts screw to screw centroid depth = `4.75cm`
* Mount screw diameter = `0.35cm`
* Mount height = `0.50cm`
* Mount depth = `0.70cm`
* Horn width = `1.95cm`
* Horn height = `0.60cm`
* Horn depth = `1.95cm`
* Horn depth offset from rear = `0.95cm`
* Horn screw to screw centroid distance = `1.00cm`
* Horn screw to centre centroid distance = `0.60cm`
* Horn screw diameter = `0.25cm`

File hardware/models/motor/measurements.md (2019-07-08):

# MG995

## Diagram

            x ______ x
           / /\  __ \ \
    H (Z) / /  \(   \\ \
         / /    \\ __)\ \ D (Y)
        x /      \ ____\ \
          \       \\___\\ \
           \       \_____\ x
            \      /     /
             \    /     /
              \  /     /
               \/_____/
                x----x
                 W (X)

## Sizes

Accuracy to +/- `0.05cm`.

* Main box width = `1.95cm`
* Main box height = `3.80cm`
* Main box depth = `3.95cm`
* Main box height with horn = `4.70cm`
* Main box mounts screw to screw centroid width = `1.00cm`
* Main box mounts screw to screw centroid height = `2.85cm`
* Main box mounts screw to screw centroid depth = `4.75cm`
* Mount screw diameter = `0.35cm`
* Mount height = `0.50cm`
* Mount depth = `0.70cm`
* Horn width = `1.95cm`
* Horn height = `0.60cm`
* Horn depth = `1.95cm`
* Horn depth offset from rear = `0.95cm`
* Horn screw to screw centroid distance = `1.00cm`
* Horn screw to centre centroid distance = `0.60cm`
* Horn screw diameter = `0.25cm`

# SM30

## Diagram

            x _______ x
           / /\  ___ \ \
    H (Z) / /  \(    \\ \
         / /    \\ ___)\ \ D (Y)
        x /      \ _____\ \
          \       \\    \\ \
           \       \\____\\ \
            \       \______\ x
             \      /      /
              \    /      /
               \  /      /
                \/______/
                 x-----x
                  W (X)

## Sizes

Accuracy to +/- `0.01cm`. (Measured using digital calipers)

* Body width = `2.80cm`
* Body height = `3.44cm`
* Body depth = `5.20cm`
* Body height with horns = `4.54cm`
* Horn diam = `2.39cm`
* Horn height = `0.26cm`
* Horn depth offset far side = `3.80cm`
* Horn screw diam = `0.30cm`
* Horn dist to body = `0.07cm`
* Mount hole dist to edge = `0.18cm`
* Mount hole diam = `0.24cm`
* Mount hole height = `1cm` (Made up)

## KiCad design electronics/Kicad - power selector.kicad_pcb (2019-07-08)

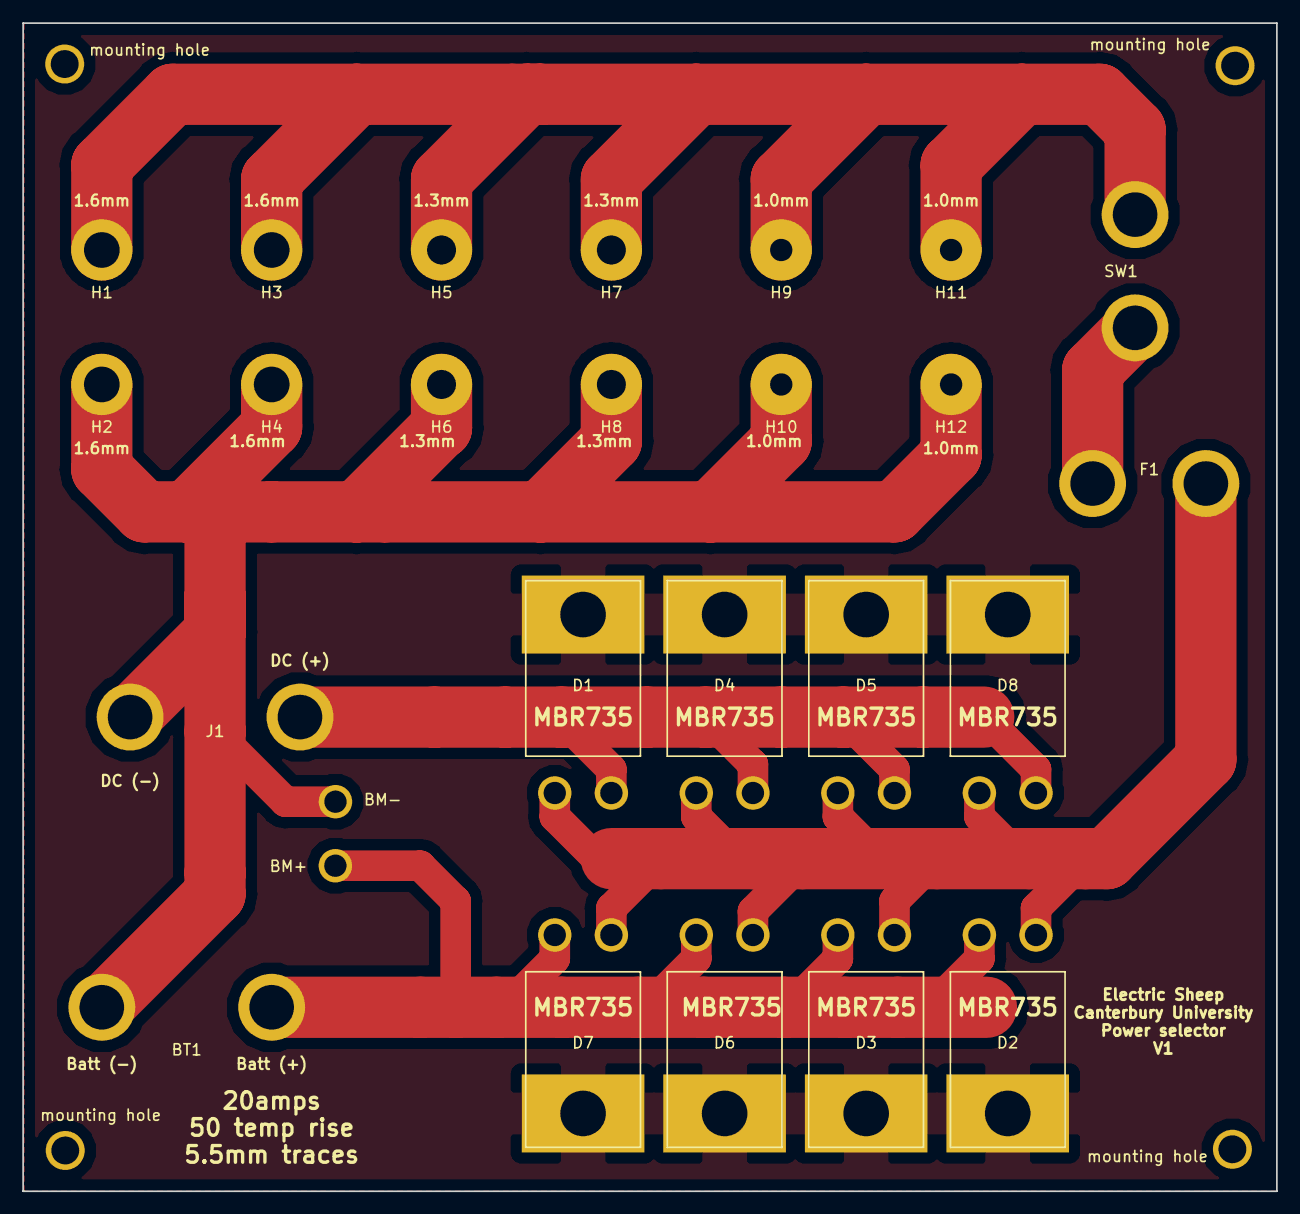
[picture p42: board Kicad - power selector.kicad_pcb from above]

Board: 2 copper layers, 112.5 x 104.8 mm, 24 parts (0 on the bottom side), 2 nets.

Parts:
BT1: Battery
D1, D2, D3, D4, D5, D6, D7, D8: MBR735
F1: Fuse
H1, H2, H3, H4: MountingHole_Pad; 1.6mm hole
H5, H6, H7, H8: MountingHole_Pad; 1.3mm
H9, H10, H11, H12: MountingHole_Pad; 1.0mm
J1: Conn_Coaxial_Power; Power
SW1: SW_DIP_x01; Switch

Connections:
unnamed: D1.4, D2.4, D3.4, D4.4, D5.4, D6.4, D7.4, D8.4
unnamed: BT1.+, BT1.-, D1.1, D1.3, D2.1, D2.3, D3.1, D3.3, D4.1, D4.3, D5.1, D5.3, D6.1, D6.3, D7.1, D7.3, D8.1, D8.3, F1.1, F1.2, H1.1, H2.1, H3.1, H4.1, H5.1, H6.1, H7.1, H8.1, H9.1, H10.1, H11.1, H12.1, J1.1, J1.2, SW1.1, SW1.2

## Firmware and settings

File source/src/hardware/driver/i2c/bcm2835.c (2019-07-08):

/* bcm2835.c
// C and C++ support for Broadcom BCM 2835 as used in Raspberry Pi
// http://elinux.org/RPi_Low-level_peripherals
// http://www.raspberrypi.org/wp-content/uploads/2012/02/BCM2835-ARM-Peripherals.pdf
//
// Author: Mike McCauley
// Copyright (C) 2011-2013 Mike McCauley
// $Id: bcm2835.c,v 1.26 2018/08/27 20:45:57 mikem Exp mikem $
*/


#include <stdlib.h>
#include <stdio.h>
#include <errno.h>
#include <fcntl.h>
#include <sys/mman.h>
#include <string.h>
#include <time.h>
#include <unistd.h>
#include <sys/types.h>

#define BCK2835_LIBRARY_BUILD
#include "bcm2835.h"

/* This define enables a little test program (by default a blinking output on pin RPI_GPIO_PIN_11)
// You can do some safe, non-destructive testing on any platform with:
// gcc bcm2835.c -D BCM2835_TEST
// ./a.out
*/
/*#define BCM2835_TEST*/

/* Uncommenting this define compiles alternative I2C code for the version 1 RPi
// The P1 header I2C pins are connected to SDA0 and SCL0 on V1.
// By default I2C code is generated for the V2 RPi which has SDA1 and SCL1 connected.
*/
/* #define I2C_V1*/

/* Physical address and size of the peripherals block
// May be overridden on RPi2
*/
uint32_t *bcm2835_peripherals_base = (uint32_t *)BCM2835_PERI_BASE;
uint32_t bcm2835_peripherals_size = BCM2835_PERI_SIZE;

/* Virtual memory address of the mapped peripherals block 
 */
uint32_t *bcm2835_peripherals = (uint32_t *)MAP_FAILED;

/* And the register bases within the peripherals block
 */
volatile uint32_t *bcm2835_gpio        = (uint32_t *)MAP_FAILED;
volatile uint32_t *bcm2835_pwm         = (uint32_t *)MAP_FAILED;
volatile uint32_t *bcm2835_clk         = (uint32_t *)MAP_FAILED;
volatile uint32_t *bcm2835_pads        = (uint32_t *)MAP_FAILED;
volatile uint32_t *bcm2835_spi0        = (uint32_t *)MAP_FAILED;
volatile uint32_t *bcm2835_bsc0        = (uint32_t *)MAP_FAILED;
volatile uint32_t *bcm2835_bsc1        = (uint32_t *)MAP_FAILED;
volatile uint32_t *bcm2835_st	       = (uint32_t *)MAP_FAILED;
volatile uint32_t *bcm2835_aux	       = (uint32_t *)MAP_FAILED;
volatile uint32_t *bcm2835_spi1        = (uint32_t *)MAP_FAILED;


/* This variable allows us to test on hardware other than RPi.
// It prevents access to the kernel memory, and does not do any peripheral access
// Instead it prints out what it _would_ do if debug were 0
 */
static uint8_t debug = 0;

/* I2C The time needed to transmit one byte. In microseconds.
 */
static int i2c_byte_wait_us = 0;

/* SPI bit order. BCM2835 SPI0 only supports MSBFIRST, so we instead 
 * have a software based bit reversal, based on a contribution by Damiano Benedetti
 */
static uint8_t bcm2835_spi_bit_order = BCM2835_SPI_BIT_ORDER_MSBFIRST;
static uint8_t bcm2835_byte_reverse_table[] = 
{
    0x00, 0x80, 0x40, 0xc0, 0x20, 0xa0, 0x60, 0xe0,
    0x10, 0x90, 0x50, 0xd0, 0x30, 0xb0, 0x70, 0xf0,
    0x08, 0x88, 0x48, 0xc8, 0x28, 0xa8, 0x68, 0xe8,
    0x18, 0x98, 0x58, 0xd8, 0x38, 0xb8, 0x78, 0xf8,
    0x04, 0x84, 0x44, 0xc4, 0x24, 0xa4, 0x64, 0xe4,
    0x14, 0x94, 0x54, 0xd4, 0x34, 0xb4, 0x74, 0xf4,
    0x0c, 0x8c, 0x4c, 0xcc, 0x2c, 0xac, 0x6c, 0xec,
    0x1c, 0x9c, 0x5c, 0xdc, 0x3c, 0xbc, 0x7c, 0xfc,
    0x02, 0x82, 0x42, 0xc2, 0x22, 0xa2, 0x62, 0xe2,
    0x12, 0x92, 0x52, 0xd2, 0x32, 0xb2, 0x72, 0xf2,
    0x0a, 0x8a, 0x4a, 0xca, 0x2a, 0xaa, 0x6a, 0xea,
    0x1a, 0x9a, 0x5a, 0xda, 0x3a, 0xba, 0x7a, 0xfa,
    0x06, 0x86, 0x46, 0xc6, 0x26, 0xa6, 0x66, 0xe6,
    0x16, 0x96, 0x56, 0xd6, 0x36, 0xb6, 0x76, 0xf6,
    0x0e, 0x8e, 0x4e, 0xce, 0x2e, 0xae, 0x6e, 0xee,
    0x1e, 0x9e, 0x5e, 0xde, 0x3e, 0xbe, 0x7e, 0xfe,
    0x01, 0x81, 0x41, 0xc1, 0x21, 0xa1, 0x61, 0xe1,
    0x11, 0x91, 0x51, 0xd1, 0x31, 0xb1, 0x71, 0xf1,
    0x09, 0x89, 0x49, 0xc9, 0x29, 0xa9, 0x69, 0xe9,
    0x19, 0x99, 0x59, 0xd9, 0x39, 0xb9, 0x79, 0xf9,
    0x05, 0x85, 0x45, 0xc5, 0x25, 0xa5, 0x65, 0xe5,
    0x15, 0x95, 0x55, 0xd5, 0x35, 0xb5, 0x75, 0xf5,
    0x0d, 0x8d, 0x4d, 0xcd, 0x2d, 0xad, 0x6d, 0xed,
    0x1d, 0x9d, 0x5d, 0xdd, 0x3d, 0xbd, 0x7d, 0xfd,
    0x03, 0x83, 0x43, 0xc3, 0x23, 0xa3, 0x63, 0xe3,
    0x13, 0x93, 0x53, 0xd3, 0x33, 0xb3, 0x73, 0xf3,
    0x0b, 0x8b, 0x4b, 0xcb, 0x2b, 0xab, 0x6b, 0xeb,
    0x1b, 0x9b, 0x5b, 0xdb, 0x3b, 0xbb, 0x7b, 0xfb,
    0x07, 0x87, 0x47, 0xc7, 0x27, 0xa7, 0x67, 0xe7,
    0x17, 0x97, 0x57, 0xd7, 0x37, 0xb7, 0x77, 0xf7,
    0x0f, 0x8f, 0x4f, 0xcf, 0x2f, 0xaf, 0x6f, 0xef,
    0x1f, 0x9f, 0x5f, 0xdf, 0x3f, 0xbf, 0x7f, 0xff
};

static uint8_t bcm2835_correct_order(uint8_t b)
{
    if (bcm2835_spi_bit_order == BCM2835_SPI_BIT_ORDER_LSBFIRST)
	return bcm2835_byte_reverse_table[b];
    else
	return b;
}

/*
// Low level register access functions
*/

/* Function to return the pointers to the hardware register bases */
uint32_t* bcm2835_regbase(uint8_t regbase)
{
    switch (regbase)
    {
	case BCM2835_REGBASE_ST:
	    return (uint32_t *)bcm2835_st;
	case BCM2835_REGBASE_GPIO:
	    return (uint32_t *)bcm2835_gpio;
	case BCM2835_REGBASE_PWM:
	    return (uint32_t *)bcm2835_pwm;
	case BCM2835_REGBASE_CLK:
	    return (uint32_t *)bcm2835_clk;
	case BCM2835_REGBASE_PADS:
	    return (uint32_t *)bcm2835_pads;
	case BCM2835_REGBASE_SPI0:
	    return (uint32_t *)bcm2835_spi0;
	case BCM2835_REGBASE_BSC0:
	    return (uint32_t *)bcm2835_bsc0;
	case BCM2835_REGBASE_BSC1:
	    return (uint32_t *)bcm2835_st;
	case BCM2835_REGBASE_AUX:
	    return (uint32_t *)bcm2835_aux;
	case BCM2835_REGBASE_SPI1:
	    return (uint32_t *)bcm2835_spi1;

    }
    return (uint32_t *)MAP_FAILED;
}

void  bcm2835_set_debug(uint8_t d)
{
    debug = d;
}

unsigned int bcm2835_version(void) 
{
    return BCM2835_VERSION;
}

/* Read with memory barriers from peripheral
 *
 */
uint32_t bcm2835_peri_read(volatile uint32_t* paddr)
{
    uint32_t ret;
    if (debug)
    {
		printf("bcm2835_peri_read  paddr %p\n", (void *) paddr);
		return 0;
    }
    else
    {
       __sync_synchronize();
       ret = *paddr;
       __sync_synchronize();
       return ret;
    }
}

/* read from peripheral without the read barrier
 * This can only be used if more reads to THE SAME peripheral
 * will follow.  The sequence must terminate with memory barrier
 * before any read or write to another peripheral can occur.
 * The MB can be explicit, or one of the barrier read/write calls.
 */
uint32_t bcm2835_peri_read_nb(volatile uint32_t* paddr)
{
    if (debug)
    {
	printf("bcm2835_peri_read_nb  paddr %p\n", paddr);
	return 0;
    }
    else
    {
	return *paddr;
    }
}

/* Write with memory barriers to peripheral
 */

void bcm2835_peri_write(volatile uint32_t* paddr, uint32_t value)
{
    if (debug)
    {
	printf("bcm2835_peri_write paddr %p, value %08X\n", paddr, value);
    }
    else
    {
        __sync_synchronize();
        *paddr = value;
        __sync_synchronize();
    }
}

/* write to peripheral without the write barrier */
void bcm2835_peri_write_nb(volatile uint32_t* paddr, uint32_t value)
{
    if (debug)
    {
	printf("bcm2835_peri_write_nb paddr %p, value %08X\n",
                paddr, value);
    }
    else
    {
	*paddr = value;
    }
}

/* Set/clear only the bits in value covered by the mask
 * This is not atomic - can be interrupted.
 */
void bcm2835_peri_set_bits(volatile uint32_t* paddr, uint32_t value, uint32_t mask)
{
    uint32_t v = bcm2835_peri_read(paddr);
    v = (v & ~mask) | (value & mask);
    bcm2835_peri_write(paddr, v);
}

/*
// Low level convenience functions
*/

/* Function select
// pin is a BCM2835 GPIO pin number NOT RPi pin number
//      There are 6 control registers, each control the functions of a block
//      of 10 pins.
//      Each control register has 10 sets of 3 bits per GPIO pin:
//
//      000 = GPIO Pin X is an input
//      001 = GPIO Pin X is an output
//      100 = GPIO Pin X takes alternate function 0
//      101 = GPIO Pin X takes alternate function 1
//      110 = GPIO Pin X takes alternate function 2
//      111 = GPIO Pin X takes alternate function 3
//      011 = GPIO Pin X takes alternate function 4
//      010 = GPIO Pin X takes alternate function 5
//
// So the 3 bits for port X are:
//      X / 10 + ((X % 10) * 3)
*/
void bcm2835_gpio_fsel(uint8_t pin, uint8_t mode)
{
    /* Function selects are 10 pins per 32 bit word, 3 bits per pin */
    volatile uint32_t* paddr = bcm2835_gpio + BCM2835_GPFSEL0/4 + (pin/10);
    uint8_t   shift = (pin % 10) * 3;
    uint32_t  mask = BCM2835_GPIO_FSEL_MASK << shift;
    uint32_t  value = mode << shift;
    bcm2835_peri_set_bits(paddr, value, mask);
}

/* Set output pin */
void bcm2835_gpio_set(uint8_t pin)
{
    volatile uint32_t* paddr = bcm2835_gpio + BCM2835_GPSET0/4 + pin/32;
    uint8_t shift = pin % 32;
    bcm2835_peri_write(paddr, 1 << shift);
}

/* Clear output pin */
void bcm2835_gpio_clr(uint8_t pin)
{
    volatile uint32_t* paddr = bcm2835_gpio + BCM2835_GPCLR0/4 + pin/32;
    uint8_t shift = pin % 32;
    bcm2835_peri_write(paddr, 1 << shift);
}

/* Set all output pins in the mask */
void bcm2835_gpio_set_multi(uint32_t mask)
{
    volatile uint32_t* paddr = bcm2835_gpio + BCM2835_GPSET0/4;
    bcm2835_peri_write(paddr, mask);
}

/* Clear all output pins in the mask */
void bcm2835_gpio_clr_multi(uint32_t mask)
{
    volatile uint32_t* paddr = bcm2835_gpio + BCM2835_GPCLR0/4;
    bcm2835_peri_write(paddr, mask);
}

/* Read input pin */
uint8_t bcm2835_gpio_lev(uint8_t pin)
{
    volatile uint32_t* paddr = bcm2835_gpio + BCM2835_GPLEV0/4 + pin/32;
    uint8_t shift = pin % 32;
    uint32_t value = bcm2835_peri_read(paddr);
    return (value & (1 << shift)) ? HIGH : LOW;
}

/* See if an event detection bit is set
// Sigh cant support interrupts yet
*/
uint8_t bcm2835_gpio_eds(uint8_t pin)
{
    volatile uint32_t* paddr = bcm2835_gpio + BCM2835_GPEDS0/4 + pin/32;
    uint8_t shift = pin % 32;
    uint32_t value = bcm2835_peri_read(paddr);
    return (value & (1 << shift)) ? HIGH : LOW;
}

uint32_t bcm2835_gpio_eds_multi(uint32_t mask)
{
    volatile uint32_t* paddr = bcm2835_gpio + BCM2835_GPEDS0/4;
    uint32_t value = bcm2835_peri_read(paddr);
    return (value & mask);
}

/* Write a 1 to clear the bit in EDS */
void bcm2835_gpio_set_eds(uint8_t pin)
{
    volatile uint32_t* paddr = bcm2835_gpio + BCM2835_GPEDS0/4 + pin/32;
    uint8_t shift = pin % 32;
    uint32_t value = 1 << shift;
    bcm2835_peri_write(paddr, value);
}

void bcm2835_gpio_set_eds_multi(uint32_t mask)
{
    volatile uint32_t* paddr = bcm2835_gpio + BCM2835_GPEDS0/4;
    bcm2835_peri_write(paddr, mask);
}

/* Rising edge detect enable */
void bcm2835_gpio_ren(uint8_t pin)
{
    volatile uint32_t* paddr = bcm2835_gpio + BCM2835_GPREN0/4 + pin/32;
    uint8_t shift = pin % 32;
    uint32_t value = 1 << shift;
    bcm2835_peri_set_bits(paddr, value, value);
}
void bcm2835_gpio_clr_ren(uint8_t pin)
{
    volatile uint32_t* paddr = bcm2835_gpio + BCM2835_GPREN0/4 + pin/32;
    uint8_t shift = pin % 32;
    uint32_t value = 1 << shift;
    bcm2835_peri_set_bits(paddr, 0, value);
}

/* Falling edge detect enable */
void bcm2835_gpio_fen(uint8_t pin)
{
    volatile uint32_t* paddr = bcm2835_gpio + BCM2835_GPFEN0/4 + pin/32;
    uint8_t shift = pin % 32;
    uint32_t value = 1 << shift;
    bcm2835_peri_set_bits(paddr, value, value);
}
void bcm2835_gpio_clr_fen(uint8_t pin)
{
    volatile uint32_t* paddr = bcm2835_gpio + BCM2835_GPFEN0/4 + pin/32;
    uint8_t shift = pin % 32;
    uint32_t value = 1 << shift;
    bcm2835_peri_set_bits(paddr, 0, value);
}

/* High detect enable */
void bcm2835_gpio_hen(uint8_t pin)
{
    volatile uint32_t* paddr = bcm2835_gpio + BCM2835_GPHEN0/4 + pin/32;
    uint8_t shift = pin % 32;
    uint32_t value = 1 << shift;
    bcm2835_peri_set_bits(paddr, value, value);
}
void bcm2835_gpio_clr_hen(uint8_t pin)
{
    volatile uint32_t* paddr = bcm2835_gpio + BCM2835_GPHEN0/4 + pin/32;
    uint8_t shift = pin % 32;
    uint32_t value = 1 << shift;
    bcm2835_peri_set_bits(paddr, 0, value);
}

/* Low detect enable */
void bcm2835_gpio_len(uint8_t pin)
{
    volatile uint32_t* paddr = bcm2835_gpio + BCM2835_GPLEN0/4 + pin/32;
    uint8_t shift = pin % 32;
    uint32_t value = 1 << shift;
    bcm2835_peri_set_bits(paddr, value, value);
}
void bcm2835_gpio_clr_len(uint8_t pin)
{
    volatile uint32_t* paddr = bcm2835_gpio + BCM2835_GPLEN0/4 + pin/32;
    uint8_t shift = pin % 32;
    uint32_t value = 1 << shift;
    bcm2835_peri_set_bits(paddr, 0, value);
}

/* Async rising edge detect enable */
void bcm2835_gpio_aren(uint8_t pin)
{
    volatile uint32_t* paddr = bcm2835_gpio + BCM2835_GPAREN0/4 + pin/32;
    uint8_t shift = pin % 32;
    uint32_t value = 1 << shift;
    bcm2835_peri_set_bits(paddr, value, value);
}
void bcm2835_gpio_clr_aren(uint8_t pin)
{
    volatile uint32_t* paddr = bcm2835_gpio + BCM2835_GPAREN0/4 + pin/32;
    uint8_t shift = pin % 32;
    uint32_t value = 1 << shift;
    bcm2835_peri_set_bits(paddr, 0, value);
}

/* Async falling edge detect enable */
void bcm2835_gpio_afen(uint8_t pin)
{
    volatile uint32_t* paddr = bcm2835_gpio + BCM2835_GPAFEN0/4 + pin/32;
    uint8_t shift = pin % 32;
    uint32_t value = 1 << shift;
    bcm2835_peri_set_bits(paddr, value, value);
}
void bcm2835_gpio_clr_afen(uint8_t pin)
{
    volatile uint32_t* paddr = bcm2835_gpio + BCM2835_GPAFEN0/4 + pin/32;
    uint8_t shift = pin % 32;
    uint32_t value = 1 << shift;
    bcm2835_peri_set_bits(paddr, 0, value);
}

/* Set pullup/down */
void bcm2835_gpio_pud(uint8_t pud)
{
    volatile uint32_t* paddr = bcm2835_gpio + BCM2835_GPPUD/4;
    bcm2835_peri_write(paddr, pud);
}

/* Pullup/down clock
// Clocks the value of pud into the GPIO pin
*/
void bcm2835_gpio_pudclk(uint8_t pin, uint8_t on)
{
    volatile uint32_t* paddr = bcm2835_gpio + BCM2835_GPPUDCLK0/4 + pin/32;
    uint8_t shift = pin % 32;
    bcm2835_peri_write(paddr, (on ? 1 : 0) << shift);
}

/* Read GPIO pad behaviour for groups of GPIOs */
uint32_t bcm2835_gpio_pad(uint8_t group)
{
  if (bcm2835_pads == MAP_FAILED)
    return 0;
  
    volatile uint32_t* paddr = bcm2835_pads + BCM2835_PADS_GPIO_0_27/4 + group;
    return bcm2835_peri_read(paddr);
}

/* Set GPIO pad behaviour for groups of GPIOs
// powerup value for all pads is
// BCM2835_PAD_SLEW_RATE_UNLIMITED | BCM2835_PAD_HYSTERESIS_ENABLED | BCM2835_PAD_DRIVE_8mA
*/
void bcm2835_gpio_set_pad(uint8_t group, uint32_t control)
{
  if (bcm2835_pads == MAP_FAILED)
    return;
  
    volatile uint32_t* paddr = bcm2835_pads + BCM2835_PADS_GPIO_0_27/4 + group;
    bcm2835_peri_write(paddr, control | BCM2835_PAD_PASSWRD);
}

/* Some convenient arduino-like functions
// milliseconds
*/
void bcm2835_delay(unsigned int millis)
{
    struct timespec sleeper;
    
    sleeper.tv_sec  = (time_t)(millis / 1000);
    sleeper.tv_nsec = (long)(millis % 1000) * 1000000;
    nanosleep(&sleeper, NULL);
}

/* microseconds */
void bcm2835_delayMicroseconds(uint64_t micros)
{
    struct timespec t1;
    uint64_t        start;
	
    if (debug)
    {
	/* Cant access sytem timers in debug mode */
	printf("bcm2835_delayMicroseconds %lld\n", (long long int) micros);
	return;
    }

    /* Calling nanosleep() takes at least 100-200 us, so use it for
    // long waits and use a busy wait on the System Timer for the rest.
    */
    start =  bcm2835_st_read();
   
    /* Not allowed to access timer registers (result is not as precise)*/
    if (start==0)
    {
	t1.tv_sec = 0;
	t1.tv_nsec = 1000 * (long)(micros);
	nanosleep(&t1, NULL);
	return;
    }

    if (micros > 450)
    {
	t1.tv_sec = 0;
	t1.tv_nsec = 1000 * (long)(micros - 200);
	nanosleep(&t1, NULL);
    }    
  
    bcm2835_st_delay(start, micros);
}

/*
// Higher level convenience functions
*/

/* Set the state of an output */
void bcm2835_gpio_write(uint8_t pin, uint8_t on)
{
    if (on)
	bcm2835_gpio_set(pin);
    else
	bcm2835_gpio_clr(pin);
}

/* Set the state of a all 32 outputs in the mask to on or off */
void bcm2835_gpio_write_multi(uint32_t mask, uint8_t on)
{
    if (on)
	bcm2835_gpio_set_multi(mask);
    else
	bcm2835_gpio_clr_multi(mask);
}

/* Set the state of a all 32 outputs in the mask to the values in value */
void bcm2835_gpio_write_mask(uint32_t value, uint32_t mask)
{
    bcm2835_gpio_set_multi(value & mask);
    bcm2835_gpio_clr_multi((~value) & mask);
}

/* Set the pullup/down resistor for a pin
//
// The GPIO Pull-up/down Clock Registers control the actuation of internal pull-downs on
// the respective GPIO pins. These registers must be used in conjunction with the GPPUD
// register to effect GPIO Pull-up/down changes. The following sequence of events is
// required:
// 1. Write to GPPUD to set the required control signal (i.e. Pull-up or Pull-Down or neither
// to remove the current Pull-up/down)
// 2. Wait 150 cycles ? this provides the required set-up time for the control signal
// 3. Write to GPPUDCLK0/1 to clock the control signal into the GPIO pads you wish to
// modify ? NOTE only the pads which receive a clock will be modified, all others will
// retain their previous state.
// 4. Wait 150 cycles ? this provides the required hold time for the control signal
// 5. Write to GPPUD to remove the control signal
// 6. Write to GPPUDCLK0/1 to remove the clock
//
// RPi has P1-03 and P1-05 with 1k8 pullup resistor
*/
void bcm2835_gpio_set_pud(uint8_t pin, uint8_t pud)
{
    bcm2835_gpio_pud(pud);
    delayMicroseconds(10);
    bcm2835_gpio_pudclk(pin, 1);
    delayMicroseconds(10);
    bcm2835_gpio_pud(BCM2835_GPIO_PUD_OFF);
    bcm2835_gpio_pudclk(pin, 0);
}

int bcm2835_spi_begin(void)
{
    volatile uint32_t* paddr;

    if (bcm2835_spi0 == MAP_FAILED)
      return 0; /* bcm2835_init() failed, or not root */
    
    /* Set the SPI0 pins to the Alt 0 function to enable SPI0 access on them */
    bcm2835_gpio_fsel(RPI_GPIO_P1_26, BCM2835_GPIO_FSEL_ALT0); /* CE1 */
    bcm2835_gpio_fsel(RPI_GPIO_P1_24, BCM2835_GPIO_FSEL_ALT0); /* CE0 */
    bcm2835_gpio_fsel(RPI_GPIO_P1_21, BCM2835_GPIO_FSEL_ALT0); /* MISO */
    bcm2835_gpio_fsel(RPI_GPIO_P1_19, BCM2835_GPIO_FSEL_ALT0); /* MOSI */
    bcm2835_gpio_fsel(RPI_GPIO_P1_23, BCM2835_GPIO_FSEL_ALT0); /* CLK */
    
    /* Set the SPI CS register to the some sensible defaults */
    paddr = bcm2835_spi0 + BCM2835_SPI0_CS/4;
    bcm2835_peri_write(paddr, 0); /* All 0s */
    
    /* Clear TX and RX fifos */
    bcm2835_peri_write_nb(paddr, BCM2835_SPI0_CS_CLEAR);

    return 1; // OK
}

void bcm2835_spi_end(void)
{  
    /* Set all the SPI0 pins back to input */
    bcm2835_gpio_fsel(RPI_GPIO_P1_26, BCM2835_GPIO_FSEL_INPT); /* CE1 */
    bcm2835_gpio_fsel(RPI_GPIO_P1_24, BCM2835_GPIO_FSEL_INPT); /* CE0 */
    bcm2835_gpio_fsel(RPI_GPIO_P1_21, BCM2835_GPIO_FSEL_INPT); /* MISO */
    bcm2835_gpio_fsel(RPI_GPIO_P1_19, BCM2835_GPIO_FSEL_INPT); /* MOSI */
    bcm2835_gpio_fsel(RPI_GPIO_P1_23, BCM2835_GPIO_FSEL_INPT); /* CLK */
}

void bcm2835_spi_setBitOrder(uint8_t order)
{
    bcm2835_spi_bit_order = order;
}

/* defaults to 0, which means a divider of 65536.
// The divisor must be a power of 2. Odd numbers
// rounded down. The maximum SPI clock rate is
// of the APB clock
*/
void bcm2835_spi_setClockDivider(uint16_t divider)
{
    volatile uint32_t* paddr = bcm2835_spi0 + BCM2835_SPI0_CLK/4;
    bcm2835_peri_write(paddr, divider);
}

void bcm2835_spi_set_speed_hz(uint32_t speed_hz)
{
	uint16_t divider = (uint16_t) ((uint32_t) BCM2835_CORE_CLK_HZ / speed_hz);
	divider &= 0xFFFE;
	bcm2835_spi_setClockDivider(divider);
}

void bcm2835_spi_setDataMode(uint8_t mode)
{
    volatile uint32_t* paddr = bcm2835_spi0 + BCM2835_SPI0_CS/4;
    /* Mask in the CPO and CPHA bits of CS */
    bcm2835_peri_set_bits(paddr, mode << 2, BCM2835_SPI0_CS_CPOL | BCM2835_SPI0_CS_CPHA);
}
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
int main(int argc, char **argv)
{
    /* Be non-destructive */
    bcm2835_set_debug(1);

    if (!bcm2835_init())
	return 1;

    /* Configure some GPIO pins fo some testing
    // Set RPI pin P1-11 to be an output
    */
    bcm2835_gpio_fsel(RPI_GPIO_P1_11, BCM2835_GPIO_FSEL_OUTP);
    /* Set RPI pin P1-15 to be an input */
    bcm2835_gpio_fsel(RPI_GPIO_P1_15, BCM2835_GPIO_FSEL_INPT);
    /*  with a pullup */
    bcm2835_gpio_set_pud(RPI_GPIO_P1_15, BCM2835_GPIO_PUD_UP);
    /* And a low detect enable */
    bcm2835_gpio_len(RPI_GPIO_P1_15);
    /* and input hysteresis disabled on GPIOs 0 to 27 */
    bcm2835_gpio_set_pad(BCM2835_PAD_GROUP_GPIO_0_27, BCM2835_PAD_SLEW_RATE_UNLIMITED|BCM2835_PAD_DRIVE_8mA);

#if 1
    /* Blink */
    while (1)
    {
	/* Turn it on */
	bcm2835_gpio_write(RPI_GPIO_P1_11, HIGH);
	
	/* wait a bit */
	bcm2835_delay(500);
	
	/* turn it off */
	bcm2835_gpio_write(RPI_GPIO_P1_11, LOW);
	
	/* wait a bit */
	bcm2835_delay(500);
    }
#endif

#if 0
    /* Read input */
    while (1)
    {
	/* Read some data */
	uint8_t value = bcm2835_gpio_lev(RPI_GPIO_P1_15);
	printf("read from pin 15: %d\n", value);
	
	/* wait a bit */
	bcm2835_delay(500);
    }
#endif

#if 0
    /* Look for a low event detection
    // eds will be set whenever pin 15 goes low
    */
    while (1)
    {
	if (bcm2835_gpio_eds(RPI_GPIO_P1_15))
	{
	    /* Now clear the eds flag by setting it to 1 */
	    bcm2835_gpio_set_eds(RPI_GPIO_P1_15);
	    printf("low event detect for pin 15\n");
	}

	/* wait a bit */
	bcm2835_delay(500);
    }
#endif

    if (!bcm2835_close())
	return 1;

    return 0;
}
#endif

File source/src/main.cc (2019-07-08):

#include "main.hh"

#include <cstdlib>
#include <cstdio>
#include <sstream>
#include <string>
#include <thread>
#include <unistd.h>

#include "behaviour/behaviour.cc"
#include "config/config.cc"
#include "hardware/driver/camera/camera.cc"
#include "localization/localization.cc"
#include "log.hh"
#include "motion/motion.cc"
#include "network/gamestate.cc"
#include "network/teamstate.cc"
#include "utils/timing.cc"
#include "version.hh"
#include "vision/lut/colour.hh"
#include "vision/vision.cc"
#include "www/webserver.cc"

Config* Main::config;
Localization* Main::loc;
Motion* Main::mot;
GameState* Main::gs;
TeamState* Main::ts;
Timing* Main::time;
Vision* Main::vis;

/**
 * main()
 *
 * Main entry point into the program, responsible for parsing the command line
 * arguments and starting the program correctly.
 *
 * @param argc Number of arguments.
 * @param argv An array of arguments.
 * @return The exit status of the program.
 **/
#ifndef TEST
int main(int argc, char** argv){
  Main::config = new Config("template.json", true);
  /* NOTE: Enable if using LUT colour space conversion. */
#if ENABLE_COLOUR_LUT == TRUE
  Colour::init();
#endif
  Main::printWelcome();
  /* Pull out program arguments */
  bool run = true;
  for(int x = 1; x < argc; x++){
    bool matched = false;
    if(argv[x] == std::string("-h") || argv[x] == std::string("--help")){
      x = Main::help(argv, argc, x);
      matched = true;
      run = false;
    }
    if(argv[x] == std::string("-m") || argv[x] == std::string("--motor")){
      x = Main::motor(argv, argc, x);
      matched = true;
      run = false;
    }
    if(!matched){
      WARNM("Argument not understood: ", argv[x]);
      WARN("Please refer to `--help`.");
      run = false;
    }
  }
  /* After processing arguments, should be still run main code? */
  if(run){
    Main::loc = new Localization();
    Main::mot = new Motion();
    Main::gs = new GameState();
    Main::ts = new TeamState();
    Main::time = new Timing();
    Main::vis = new Vision();
    /* Run main threads */
    std::thread mainThread(Main::mainThread);
    std::thread hwThread(Main::hwThread);
    std::thread wwwThread(Main::wwwThread);
    std::thread gameThread(Main::gameThread);
    std::thread teamThread(Main::teamThread);
    /* Wait for them to finish */
    mainThread.join();
    LOG("Main thread finished.");
    hwThread.join();
    LOG("Hardware thread finished.");
    wwwThread.join();
    LOG("Server thread finished.");
    gameThread.join();
    LOG("Game thread finished.");
    teamThread.join();
    LOG("Team thread finished.");
  }else{
    LOG("Not running program due to parameters given.");
  }
  return EXIT_SUCCESS;
}
#endif

void Main::printWelcome(){
  printf(
    "\033[1;32m%s\033[0m by \033[0;36m%s\033[0m\n",
    config->getString("app.name").c_str(),
    config->getString("app.author").c_str()
  );
  printf("\033[1;35mBuilt:\033[0m %s @ %s\n", __DATE__, __TIME__);
  printf("\033[1;35mCommit:\033[0m %s\n", GitHash());
}

int Main::help(char** argv, int argc, int x){
  printf("./robot [OPT]\n");
  printf("\n");
  printf("  OPTions\n");
  printf("\n");
  printf("    -h  --help     Display this help\n");
  printf("    -m  --motor    Directly control motor\n");
  printf("                     <HEX> Motor ID\n");
  printf("                     <INT> Number of parameters\n");
  printf("                     <HEX> Command\n");
  printf("                     <HEX> [HEX] Parameters\n");
  printf("                     <BOL> Wait for response?\n");
  printf("\n");
  printf("  Values\n");
  printf("\n");
  printf("    INT  32 bit integer (i.e, 79, 0, -2078)\n");
  printf("    HEX  Double digit hex (i.e. A0, 00, 67)\n");
  printf("    BOL  Boolean value (i.e. 1 = true, 0 = false)\n");
  return x;
}

int Main::motor(char** argv, int argc, int x){
  ++x;
  /* Check at least minimum number of arguments */
  if(argc - x < 4){
    WARNI("Minimum arguments is 4, found ", argc - x);
    return argc;
  }
  /* Convert arguments */
  int tmp;
  std::stringstream ss;
  SmartController::Packet pkt;
  ss << std::hex << argv[x++];
  ss >> pkt.id;
  ss.clear();
  ss << argv[x++];
  ss >> pkt.numParam;
  ss.clear();
  /* TODO: Check whether we have enough arguments left for params. */
  ss << std::hex << argv[x++];
  ss >> tmp;
  pkt.cmd = (SmartController::CMD)tmp;
  ss.clear();
  unsigned char param[*config->getInt("motor.smart.max-return-data").get()];
  for(int i = 0; i < pkt.numParam; i++){
    ss << std::hex << argv[x++];
    ss >> tmp;
    param[i] = (unsigned char)tmp;
    ss.clear();
  }
  pkt.param = param;
  ss << argv[x++];
  ss >> tmp;
  pkt.response = tmp > 0;
  ss.clear();
  /* Start controller */
  SmartController* sc = new SmartController(
    config->getString("motor.smart.interface-a").c_str()
  );
  sc->openPort();
  if(!sc->isActive()){
    WARN("Failed to open port");
  }
  sc->startComms();
  if(!sc->isActive()){
    WARN("Failed to start communication");
  }
  /* Send packet how it was requested */
  if(pkt.response){
    /* Send packet */
    pkt = sc->writePacket(pkt);
    /* Print packet */
    LOGB("ID         -> ", pkt.id);
    LOGB("Num params -> ", pkt.numParam);
    LOGB("Status     -> ", pkt.cmd);
    for(int i = 0; i < pkt.numParam; i++){
      LOGB("Param      -> ", pkt.param[i]);
    }
  }else{
    /* Send packet */
    sc->writePacket(pkt, true);
    LOG("Packet sense, not waiting for response");
  }
  /* Stop controller */
  sc->closePort();
  return x;
}

void Main::mainThread(){
  Camera* cam = new Camera();
  if(cam->isRunning()){
    cam->update();
  }
  std::thread* visThread = NULL;
  while(cam->isRunning()){
    Main::time->eventStart("vision", "cam-update");
    cam->update();
    Main::time->eventEnd("vision", "cam-update");
    Main::time->eventStart("vision", "vis-preprocess");
    Main::vis->preprocess(cam->getImage());
    Main::time->eventEnd("vision", "vis-preprocess");
    Main::time->eventStart("vision", "vis-process");
    if(visThread != NULL){
      visThread->join();
      delete(visThread);
    }else{
      WARN("Unable to create vision thread.");
    }
    visThread = new(nothrow) std::thread(Main::visThread);
    Main::time->eventEnd("vision", "vis-process");
    Main::time->loopTick("vision");
  }
  cam->close();
}

void Main::visThread(){
  Main::vis->process();
}
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

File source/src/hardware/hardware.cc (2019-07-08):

#include "hardware.hh"

#include "../log.hh"
#include "driver/gpio/gpio.cc"
#include "driver/i2c/gyro.cc"
#include "driver/serial/smartcontroller.cc"
//#include "motor/fs6535m.cc"
//#include "motor/mg995.cc"
#include "motor/sm30.cc"

Hardware::Hardware(){
  numMotors = *Main::config->getInt("motor.num-motors").get();
  motors = (Motor**)malloc(numMotors * sizeof(Motor*));
  running = true;
  LOG("Initializing IMU");
  if(*Main::config->getInt("gyro.active").get() > 0){
    gyro = new Gyro();
  }else{
    gyro = NULL;
  }
  LOG("Initializing GPIO buttons");
  /* Setup buttons correctly */
  GPIO::init();
  playButton  = new GPIO("playButton",  (GPIO::PIN)27, GPIO::VOLTAGE::V5, GPIO::CAPABILITY::IN);
  relaxButton = new GPIO("relaxButton", (GPIO::PIN)28, GPIO::VOLTAGE::V5, GPIO::CAPABILITY::IN);
  LOG("Initializing PWM controller");
  #if RPI == 1
    /* Setup PWM servo controller */
//    if(*Main::config->getInt("motor.pwm.active").get() > 0){
      pwm = new PCA9685Servo();
//      pwm->SetLeftUs(*Main::config->getInt("motor.pwm.fs6535m.pulse-low").get());
//      pwm->SetRightUs(*Main::config->getInt("motor.pwm.fs6535m.pulse-high").get());
//    }else{
//      pwm = NULL;
//    }
  #else
  pwm = NULL;
  #endif
  /* Setup smart controller communications */
  if(*Main::config->getInt("motor.smart.active").get() > 0){
    LOGM("Open port on -> ", Main::config->getString("motor.smart.interface-a").c_str());
    sca = new SmartController(
      Main::config->getString("motor.smart.interface-a").c_str()
    );
    sca->openPort();
    if(!sca->isActive()){
      running = false;
      WARN("Failed to open port");
    }
    sca->startComms();
    if(!sca->isActive()){
      running = false;
      WARN("Failed to start communication");
    }
//    LOGM("Open port on -> ", Main::config->getString("motor.smart.interface-b").c_str());
//    scb = new SmartController(
//      Main::config->getString("motor.smart.interface-b").c_str()
//    );
//    scb->openPort();
//    if(!scb->isActive()){
//      running = false;
//      WARN("Failed to open port");
//    }
//    scb->startComms();
//    if(!scb->isActive()){
//      running = false;
 //     WARN("Failed to start communication");
 //   }
  }else{
    sca = NULL;
//    scb = NULL;
  }
  /* Setup motors */
  motors[0]  = new SM30(Motor::TYPE::MG995, Motor::POSITION::NECK_PITCH,           "neck-pitch"          );
  motors[1]  = new SM30(Motor::TYPE::MG995, Motor::POSITION::NECK_YAW,             "neck-yaw"            );
  motors[2]  = new SM30(Motor::TYPE::MG995, Motor::POSITION::SHOULDER_PITCH_LEFT,  "shoulder-pitch-left" );
  motors[3]  = new SM30(Motor::TYPE::MG995, Motor::POSITION::SHOULDER_PITCH_RIGHT, "shoulder-pitch-right");
  motors[4]  = new SM30(Motor::TYPE::MG995, Motor::POSITION::SHOULDER_ROLL_LEFT,   "shoulder-roll-left"  );
  motors[5]  = new SM30(Motor::TYPE::MG995, Motor::POSITION::SHOULDER_ROLL_RIGHT,  "shoulder-roll-right" );
  motors[6]  = new SM30(Motor::TYPE::MG995, Motor::POSITION::ELBOW_PITCH_LEFT,     "elbow-pitch-left"    );
  motors[7]  = new SM30(Motor::TYPE::MG995, Motor::POSITION::ELBOW_PITCH_RIGHT,    "elbow-pitch-right"   );
  motors[8]  = new SM30(Motor::TYPE::SM30,  Motor::POSITION::HIP_YAW_LEFT,         "hip-yaw-left"        );
  motors[9]  = new SM30(Motor::TYPE::SM30,  Motor::POSITION::HIP_YAW_RIGHT,        "hip-yaw-right"       );
  motors[10] = new SM30(Motor::TYPE::SM30,  Motor::POSITION::HIP_ROLL_LEFT,        "hip-roll-left"       );
  motors[11] = new SM30(Motor::TYPE::SM30,  Motor::POSITION::HIP_ROLL_RIGHT,       "hip-roll-right"      );
  motors[12] = new SM30(Motor::TYPE::SM30,  Motor::POSITION::HIP_PITCH_LEFT,       "hip-pitch-left"      );
  motors[13] = new SM30(Motor::TYPE::SM30,  Motor::POSITION::HIP_PITCH_RIGHT,      "hip-pitch-right"     );
  motors[14] = new SM30(Motor::TYPE::SM30,  Motor::POSITION::KNEE_PITCH_LEFT,      "knee-pitch-left"     );
  motors[15] = new SM30(Motor::TYPE::SM30,  Motor::POSITION::KNEE_PITCH_RIGHT,     "knee-pitch-right"    );
  motors[16] = new SM30(Motor::TYPE::SM30,  Motor::POSITION::ANKLE_PITCH_LEFT,     "ankle-pitch-left"    );
  motors[17] = new SM30(Motor::TYPE::SM30,  Motor::POSITION::ANKLE_PITCH_RIGHT,    "ankle-pitch-right"   );
  motors[18] = new SM30(Motor::TYPE::SM30,  Motor::POSITION::ANKLE_ROLL_LEFT,      "ankle-roll-left"     );
  motors[19] = new SM30(Motor::TYPE::SM30,  Motor::POSITION::ANKLE_ROLL_RIGHT,     "ankle-roll-right"    );
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

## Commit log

2019-07-08 Add hardware source files
    [ankle-complete.scad, ankle-config.scad, ankle-left.scad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]
2019-07-08 Add stripped source
    [ankle-complete.scad.stl, ankle-left.scad.stl, ankle-right.scad.stl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]
2019-07-08 Add power PBC to release
    [Kicad - power selector.kicad_pcb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]
2019-07-08 Power PCB documentation
2019-07-08 Add diodes to component list
2019-07-14 Stand-in for assembly instructions
2019-07-14 BOM and discussion
